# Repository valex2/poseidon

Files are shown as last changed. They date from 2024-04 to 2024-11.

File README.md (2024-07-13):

# poseidon
Stanford Robosub 🏄‍♂️🐳🌊 Electrical Subsystem Repository

[Website](https://www.stanfordrobosub.org/)

# Important notes
## Thrusters
DO NOT RUN THRUSTERS AT FULL POWER FOR THE TIME BEING - 20 to 30% max

DO NOT RUN FOR MORE THAN 10 SECONDS WHILE OUTSIDE OF WATER

## Comms
We are using a Teensy 4.0 that communicates with the Orin over a serial port.

Use serial library in Python, and write as follows:
> portName.write(b"thruster_number delay_value")

### Thruster PWM Assignment
- 1100 us is full reverse thrust
- 1500 us is off
- 1900 us is full forward thrust

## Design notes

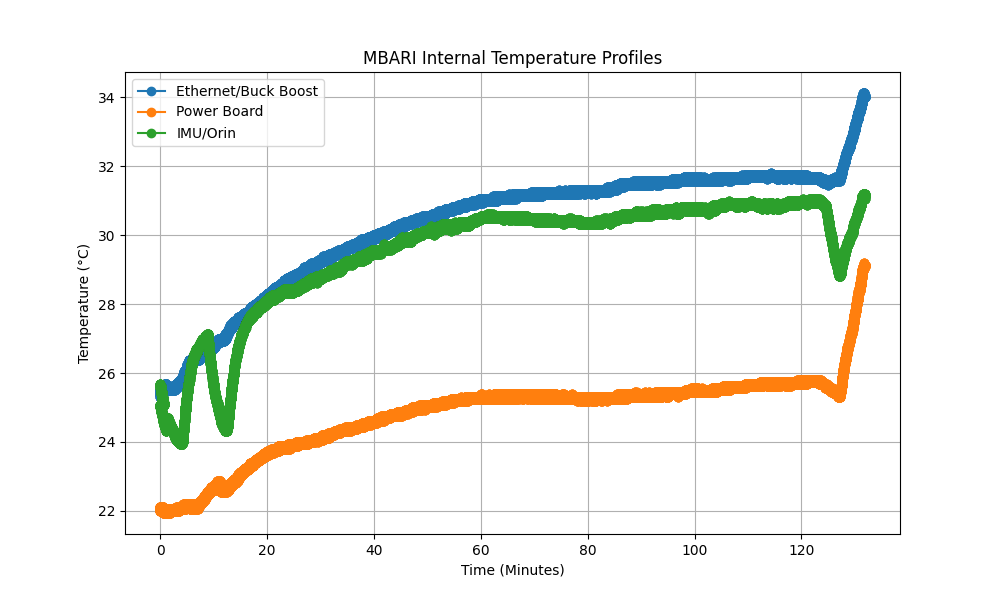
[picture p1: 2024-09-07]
CodeDev/MBARI_temperature_profiles.png

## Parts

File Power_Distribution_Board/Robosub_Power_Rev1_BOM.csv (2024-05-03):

# | Reference | Qty | Value | Footprint | DNP | Supplier 1 | Supplier 1 S/N | MFR | MFR S/N
1 | C1, C2 | 4 | 0.1u | Capacitor_SMD:C_0805_2012Metric_Pad1.18x1.45mm_HandSolder |  | https://www.digikey.com/en/products/detail/yageo/CC0805KRX7R9BB104/302874 | 311-1140-1-ND | YAGEO | CC0805KRX7R9BB104
2 | C3, C4 | 4 | 1uF | Capacitor_SMD:C_1812_4532Metric_Pad1.57x3.40mm_HandSolder |  | https://www.digikey.com/en/products/detail/knowles-syfer/1812Y2000105KSTWS2/18879756 | 1608-1812Y2000105KSTWS2CT-ND | Knowles Syfer | 1812Y2000105KSTWS2
3 | C5, C6 | 4 | 1u (electrolytic) | Robosub Lib:UCB1V0R1MCL1GS |  | https://www.digikey.com/en/products/detail/nichicon/UCB1V0R1MCL1GS/3974069 | 493-9956-1-ND | Nichicon | UCB1V0R1MCL1GS
4 | CR1 | 2 | SBRT15U50SP5-13 | SBRT15U50SP5_13:POWERDI5_DIO |  | https://www.digikey.com/en/products/detail/diodes-incorporated/SBRT15U50SP5-13/4567773 | SBRT15U50SP5-13DICT-ND | Diodes Incorporated | SBRT15U50SP5-13
5 | D1 | 2 | 1SMA5931BT3 | Diode_SMD:D_SMA |  | https://www.digikey.com/en/products/detail/onsemi/SZ1SMA5931BT3G/8538966 | SZ1SMA5931BT3GOSCT-ND | onsemi | SZ1SMA5931BT3G
6 | D2, D3 | 4 | IR26-21C_L110_TR8 | LED_SMD:LED_1206_3216Metric |  | https://www.digikey.com/en/products/detail/everlight-electronics-co-ltd/ir26-21c-l110-tr8/2675848 | 1080-1357-1-ND | Everlight Electronics Co Ltd | IR26-21C/L110/TR8
7 | H1, H2, H3, H4 | 8 | MountingHole | MountingHole:MountingHole_3.2mm_M3
8 | J1, J2, J3, J4, J5, J6, J7, J8, J9, J10 | 14 | 1135333 | 1135333_1:PHOENIX_1135333 |  | https://www.digikey.com/en/products/detail/phoenix-contact/1135333/17936877 | 277-1135333CT-ND | Pheonix Contact | SPT-THR 2,5/ 2-V-5,0 P20 R32
9 | J14 | 2 | Conn_01x04 | Connector_PinHeader_2.54mm:PinHeader_1x04_P2.54mm_Vertical
10 | JP4, JP5 | 4 | SolderJumper_2_Open | Jumper:SolderJumper-2_P1.3mm_Open_Pad1.0x1.5mm
11 | L1 | 2 | 74477420 | Robosub Lib:IND_5848-WE-PD2_WRE |  | https://www.digikey.com/en/products/detail/würth-elektronik/74477420/1638683 | 732-1278-1-ND | Würth Elektronik | 74477420
12 | R1, R3, R4 | 6 | 10k | Resistor_SMD:R_0805_2012Metric_Pad1.20x1.40mm_HandSolder |  | https://www.digikey.com/en/products/detail/yageo/RC0805FR-0710KL/727535 | 311-10.0KCRCT-ND | YAGEO | RC0805FR-0710KL
13 | R2 | 2 | 3k | Resistor_SMD:R_0805_2012Metric_Pad1.20x1.40mm_HandSolder |  | https://www.digikey.com/en/products/detail/te-connectivity-passive-product/CRG0805F3K0/2380900 | A126368CT-ND | TE Connectivity Passive Product | CRG0805F3K0
14 | R5 | 2 | 10 | Resistor_SMD:R_0805_2012Metric_Pad1.20x1.40mm_HandSolder |  | https://www.digikey.com/en/products/detail/yageo/RC0805FR-0710RL/727534 | 311-10.0CRCT-ND | YAGEO | RC0805FR-0710RL
15 | R6, R7, R8 | 6 | 100 | Resistor_SMD:R_0805_2012Metric_Pad1.20x1.40mm_HandSolder |  | https://www.digikey.com/en/products/detail/yageo/RC0805FR-07100RL/727543 | 311-100CRCT-ND | YAGEO | RC0805FR-07100RL
16 | R9 | 2 | 0 (100A) | Resistor_SMD:R_2512_6332Metric_Pad1.40x3.35mm_HandSolder |  | https://www.digikey.com/en/products/detail/bourns-inc./CSS2H-2512C-000E/16357993?gad_source=1 | 118-CSS2H-2512C-000ECT-ND | Bourns Inc. | CSS2H-2512C-000E
17 | U1 | 2 | INA300AIDSQT | Robosub Lib:SON40P200X200X80-11N |  | https://www.digikey.com/en/products/detail/texas-instruments/INA300AIDSQT/4759519 | 296-37474-1-ND | Texas Instruments | INA300AIDSQT
18 | U2 | 2 | SN74LVC1G97DBVR | Robosub Lib:SOT95P280X145-6N |  | https://www.digikey.com/en/products/detail/texas-instruments/SN74LVC1G97DBVR/571196 | 296-15581-1-ND | Texas Instruments | SN74LVC1G97DBVR
19 | U3 | 2 | AUIR3241STR | Robosub Lib:SOIC127P600X175-8N_AUIR3241STR |  | https://www.digikey.com/en/products/detail/infineon-technologies/auir3241str/7428056 | AUIR3241SCT-ND | Infineon Technologies | AUIR3241STR
20 | U4, U5, U6 | 6 | BSC0702LSATMA1 | Robosub Lib:BSC0702LSATMA1 |  | https://www.digikey.com/en/products/detail/infineon-technologies/BSC0702LSATMA1/7323968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 | 448-BSC0702LSATMA1CT-ND | Infineon Technologies | BSC0702LSATMA1
21 | U7, U8 | 3 | NVTR01P02LT1G | Robosub Lib:SOT-23-3_1P4X3P040_ONS |  | https://www.digikey.com/en/products/detail/onsemi/NVTR01P02LT1G/3062562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 | NVTR01P02LT1GOSCT-ND | onsemi | NVTR01P02LT1G
22 | WSLP59312L000FEA_1, WSLP59312L000FEA_2 | 4 | 2mOhm | WSLP59312L000FEA:RES_WSLP5931_.002OHM_VIS |  | https://www.digikey.com/en/products/detail/vishay-dale/WSLP59312L000FEA/5215934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 | 541-10013-1-ND | Vishay Dale | WSLP59312L000FEA
23 | Hall effect | 1 |  |  |  | https://www.digikey.com/en/products/detail/littelfuse-inc/55140-3H-02-A/565513 | 55140-3H-02-A-ND | Littelfuse Inc. | 55140-3H-02-A
24 | Magnet | 1 |  |  |  | https://www.digikey.com/en/products/detail/littelfuse-inc/H-58-MAGNET/10269030 | F12127-ND | Littelfuse Inc. | H-58-MAGNET

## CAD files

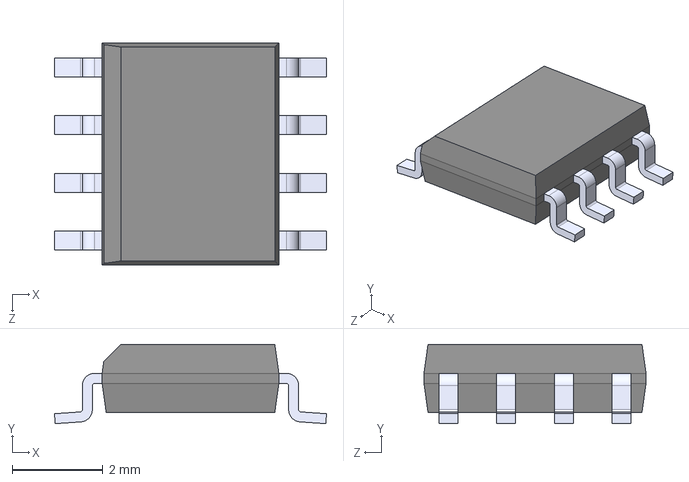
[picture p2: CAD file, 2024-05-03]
Power_Distribution_Board/EDA/AUIR3241STR/AUIR3241STR.step
6.00 x 1.75 x 4.90 mm

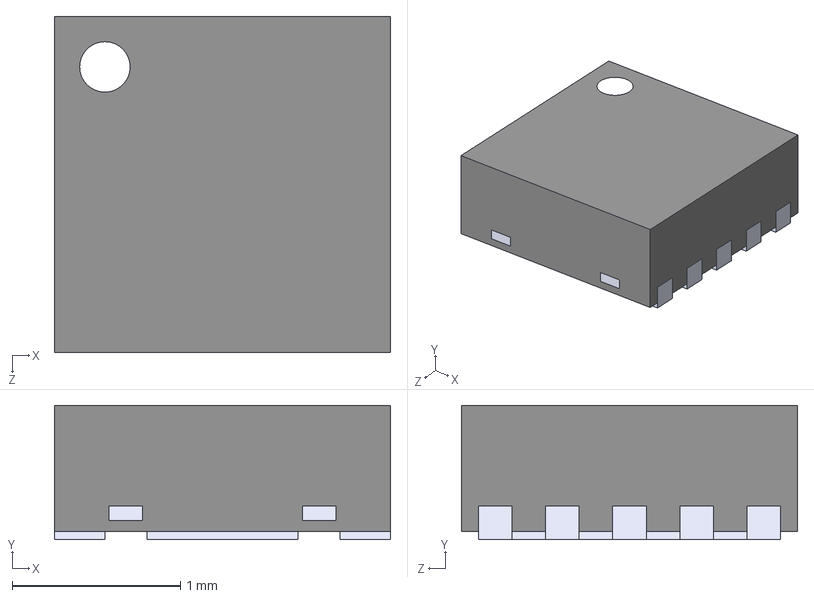
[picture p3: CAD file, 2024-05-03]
Power_Distribution_Board/EDA/INA300AIDSQT/INA300AIDSQT.step
2.00 x 0.8 x 2.00 mm

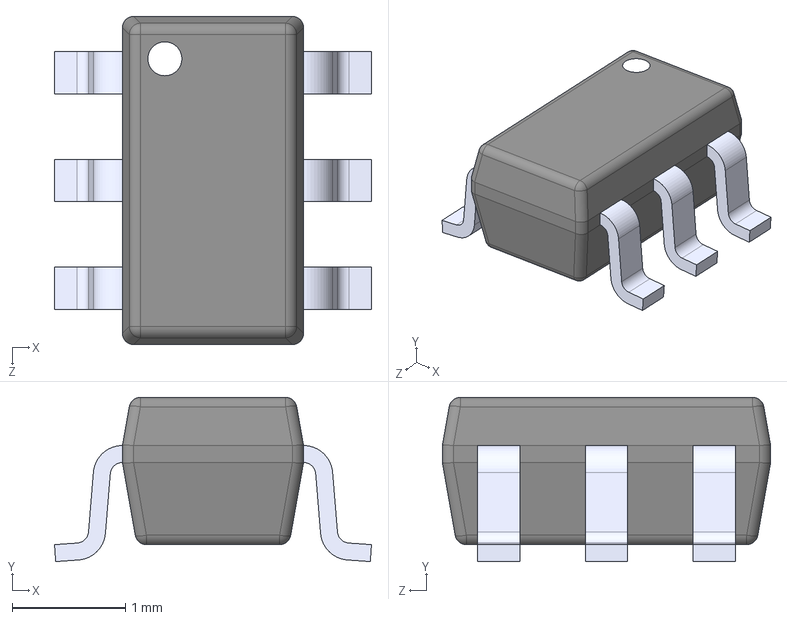
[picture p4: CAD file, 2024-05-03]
Power_Distribution_Board/EDA/SN74LVC1G97DBVR/SN74LVC1G97DBVR.step
2.80 x 1.45 x 2.90 mm

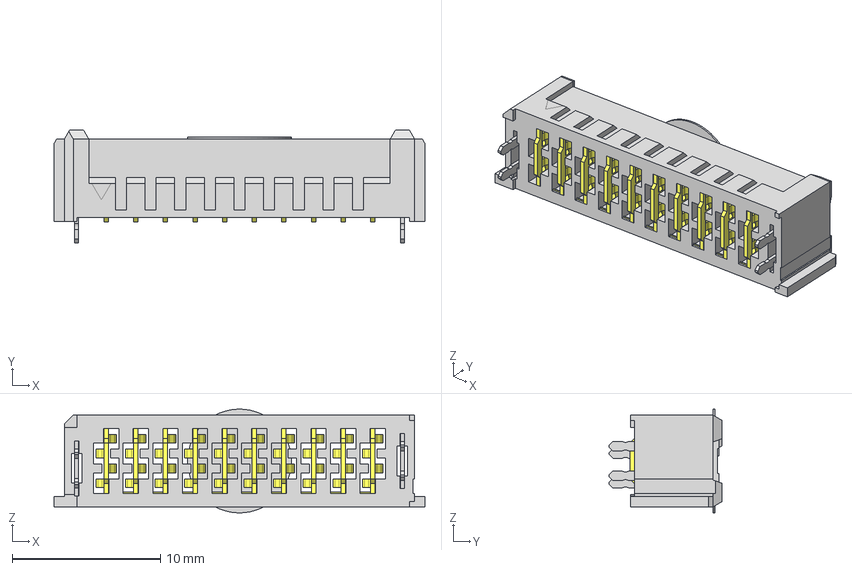
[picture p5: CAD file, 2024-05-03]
Power_Distribution_Board/EDA/UMPS_10_05_5_L_V_S_W_TR/UMPS-10-05.5-L-V-S-W-TR.step
25.1 x 7.60 x 7.01 mm
10-05.5--W_BODY
UMPS-10-05.5-S_PINS
10-05.5-S_PINS2
K-DOT-0.276-.005_KAPTON

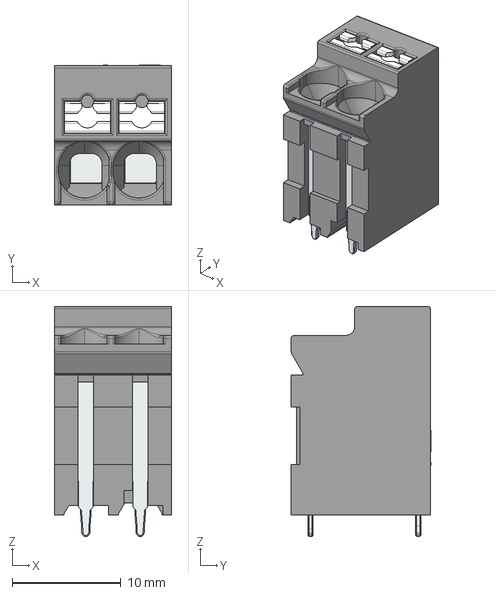
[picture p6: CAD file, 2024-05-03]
Power_Distribution_Board/EDA/1135333/1135333.step
10.8 x 12.8 x 21.2 mm

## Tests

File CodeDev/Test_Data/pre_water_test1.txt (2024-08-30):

1472,22.75,21.94,21.94
1541,22.75,21.94,21.94
1592,22.75,21.94,21.94
1642,22.75,21.94,21.94
1693,22.75,21.94,21.94
1743,22.75,21.94,21.94
1794,22.75,21.94,21.94
1844,22.75,21.94,21.94
1895,22.75,21.94,21.94
1945,22.75,21.94,21.94
1996,22.75,21.94,21.94
2046,22.75,21.94,21.94
2097,22.75,21.94,21.94
2147,22.75,21.94,21.94
2198,22.75,22.00,21.94
2248,22.75,22.00,21.94
2299,22.75,22.00,21.94
2349,22.75,22.00,21.94
2400,22.75,22.00,21.94
2450,22.81,21.94,21.94
2500,22.81,21.94,21.94
2551,22.81,21.94,21.94
2601,22.81,21.94,21.94
2652,22.81,21.94,21.94
2701,22.75,22.00,21.94
2752,22.75,22.00,21.94
2807,22.75,22.00,21.94
2858,22.75,22.00,21.94
2908,22.75,22.00,21.94
2958,22.75,21.94,21.94
3008,22.75,21.94,21.94
3058,22.75,21.94,21.94
3108,22.75,21.94,21.94
3159,22.75,21.94,21.94
3209,22.75,21.94,21.94
3259,22.75,21.94,21.94
3309,22.75,21.94,21.94
3359,22.75,21.94,21.94
3410,22.81,21.94,21.94
3460,22.81,22.00,21.94
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

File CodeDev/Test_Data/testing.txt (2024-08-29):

2515,25.31,24.94,25.12
2584,25.31,24.94,25.12
2634,25.31,24.94,25.12
2687,25.31,24.94,25.12
2737,25.31,24.94,25.12
2788,25.31,24.94,25.12
2838,25.31,24.94,25.12
2890,25.31,24.94,25.12
2941,25.31,24.94,25.12
2991,25.31,24.94,25.12
3042,25.31,24.88,25.12
3093,25.31,24.88,25.12
3143,25.31,24.88,25.12
3194,25.31,24.88,25.12
3245,25.31,24.88,25.12
3295,25.25,24.88,25.12
3346,25.25,24.88,25.12
3396,25.25,24.88,25.12
3447,25.25,24.88,25.12
3498,25.25,24.88,25.12
3548,25.31,24.94,25.12
3599,25.31,24.94,25.12
3649,25.31,24.94,25.19
3700,25.31,24.94,25.19
3750,25.31,24.94,25.19
3800,25.31,24.94,25.19
3851,25.31,24.94,25.19
3906,25.31,24.94,25.12
3957,25.31,24.94,25.12
4008,25.25,24.94,25.12
4058,25.25,24.88,25.12
4108,25.25,24.88,25.12
4159,25.25,24.88,25.12
4209,25.25,24.88,25.12
4260,25.25,24.88,25.12
4310,25.25,24.88,25.12
4360,25.25,24.88,25.12
4410,25.25,24.88,25.12
4461,25.25,24.88,25.12
4511,25.31,24.88,25.12
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

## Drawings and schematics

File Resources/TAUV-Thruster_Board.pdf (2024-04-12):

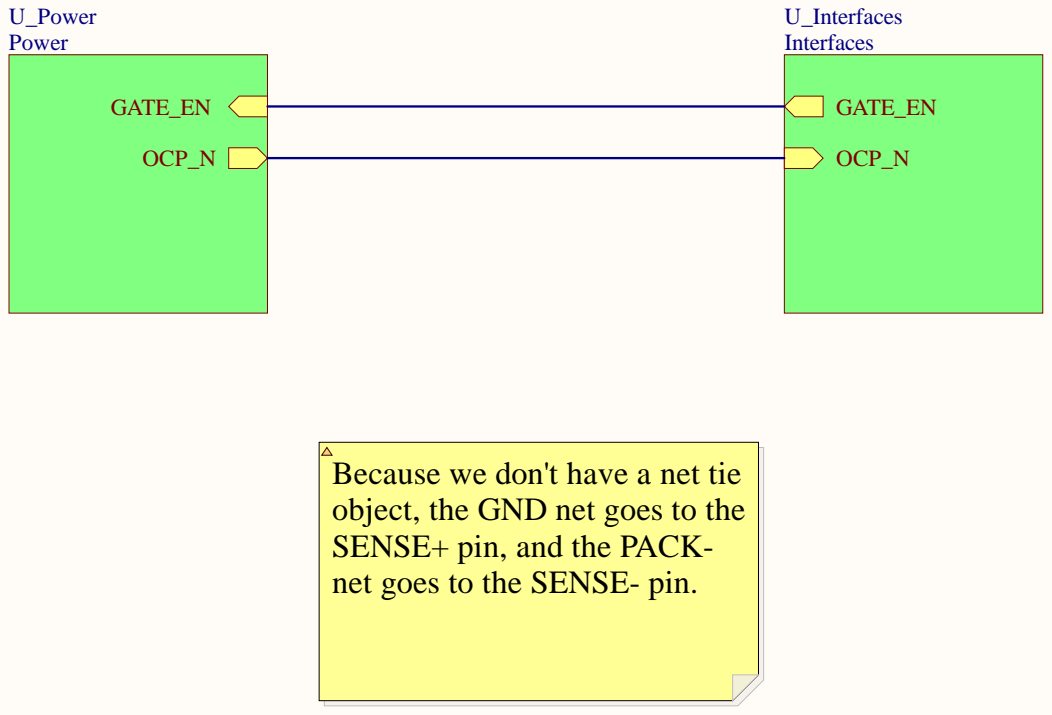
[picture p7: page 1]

Because we don't have a net tie
object, the GND net goes to the
SENSE+ pin, and the PACK-
net goes to the SENSE- pin.

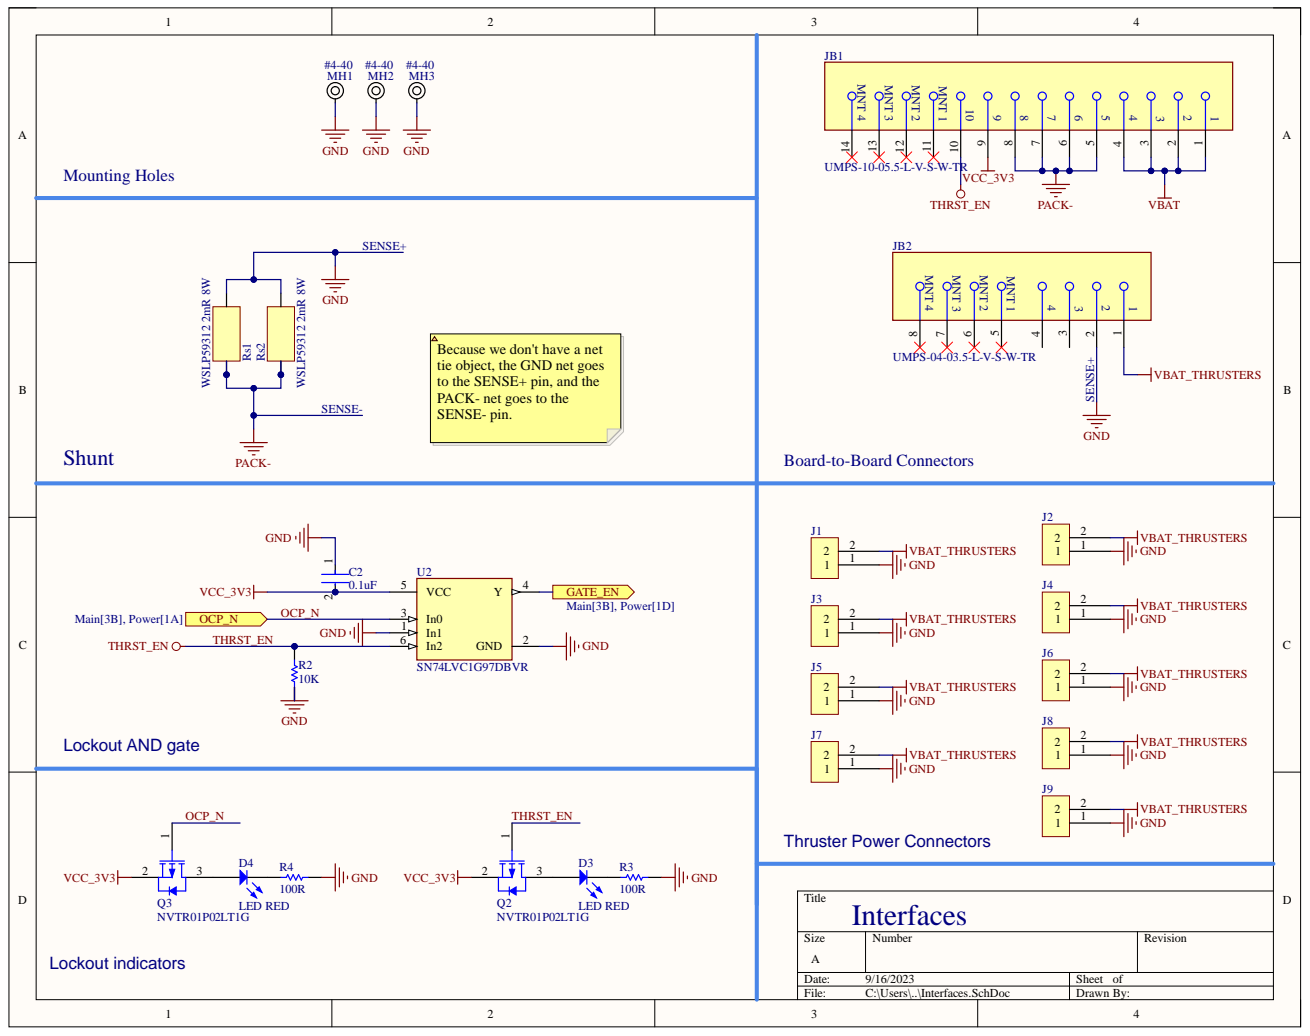
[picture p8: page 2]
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

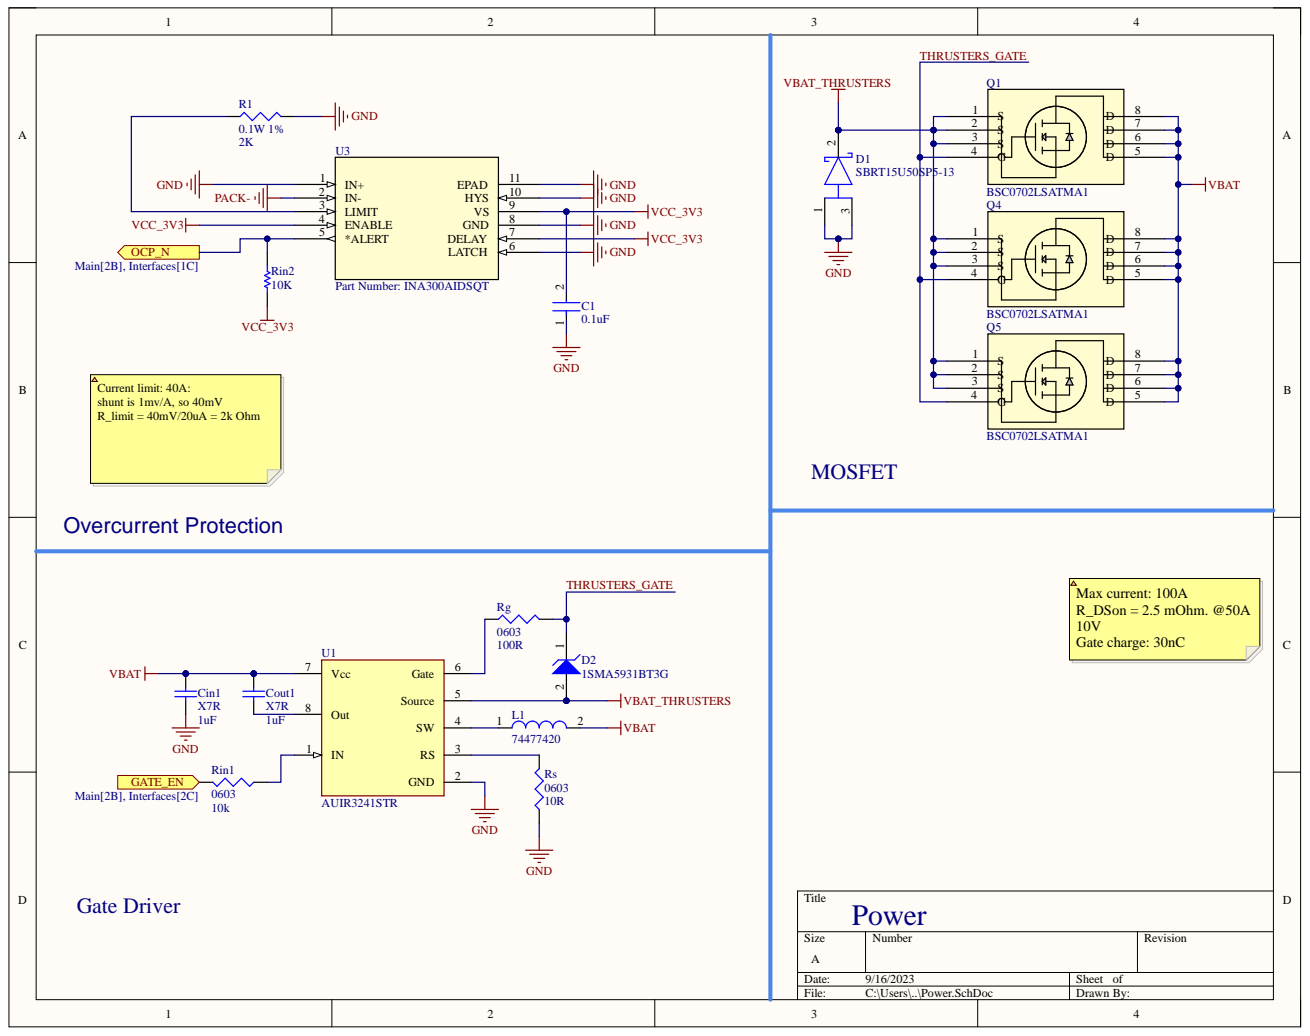
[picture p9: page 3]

LIMIT 3

*ALERT 5

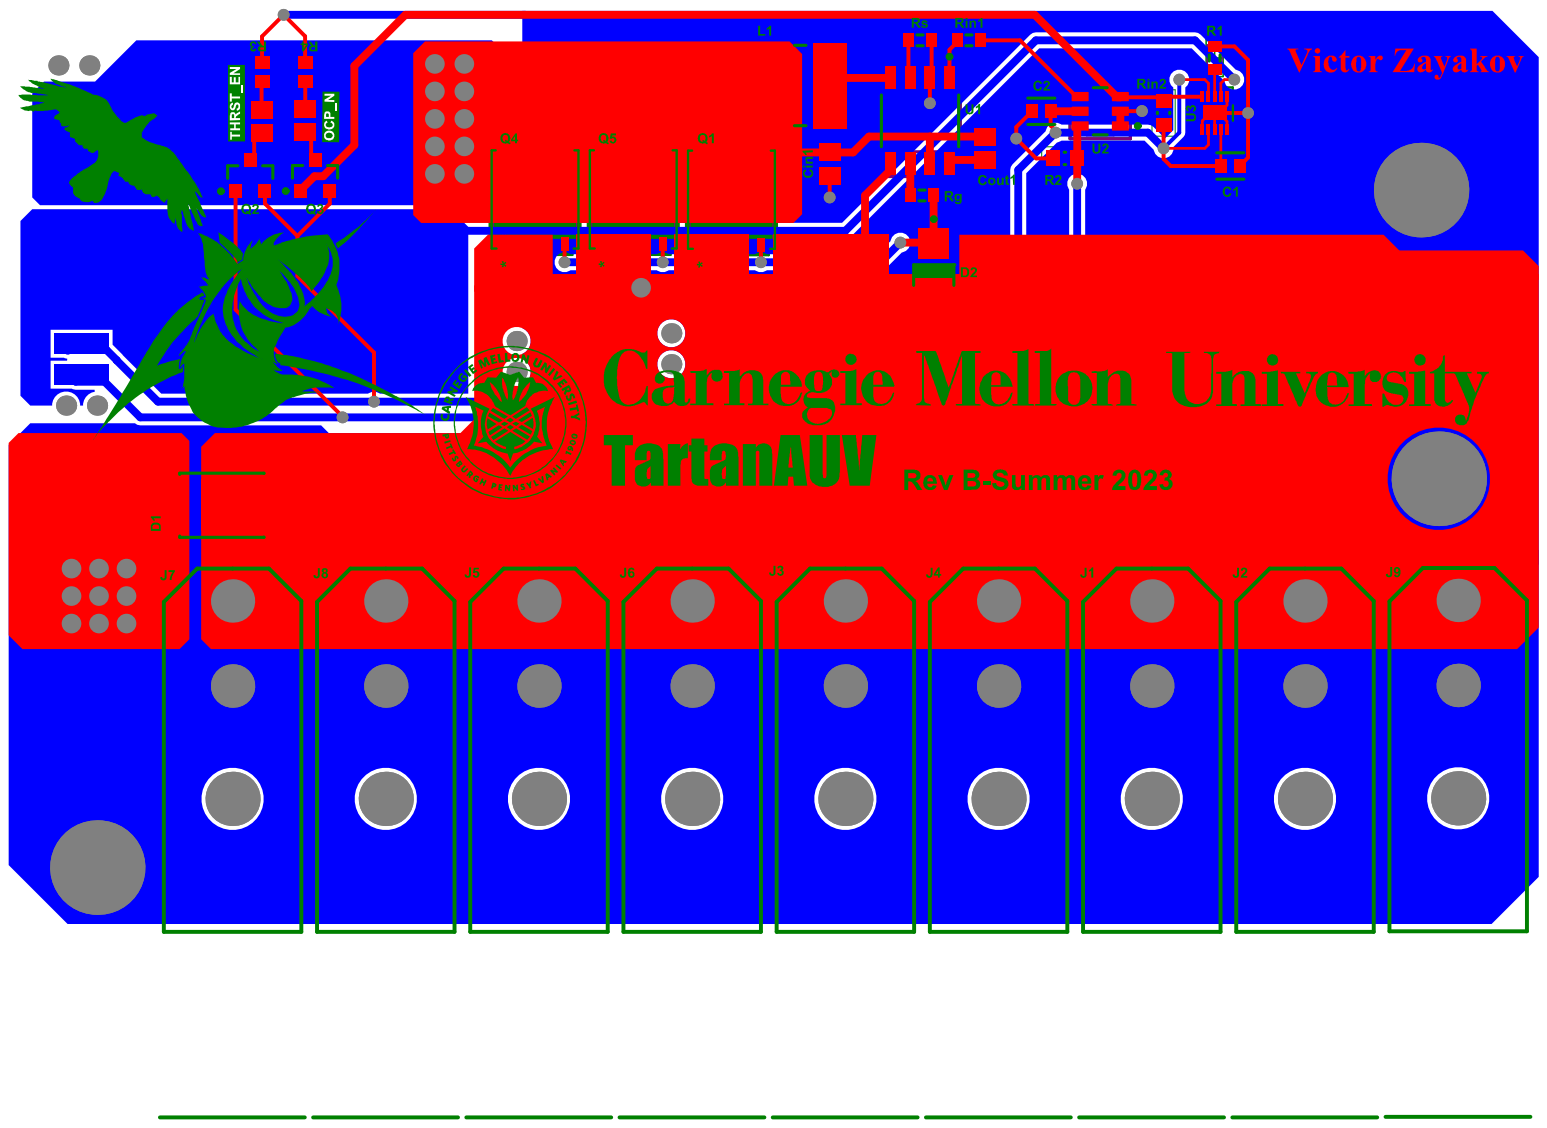
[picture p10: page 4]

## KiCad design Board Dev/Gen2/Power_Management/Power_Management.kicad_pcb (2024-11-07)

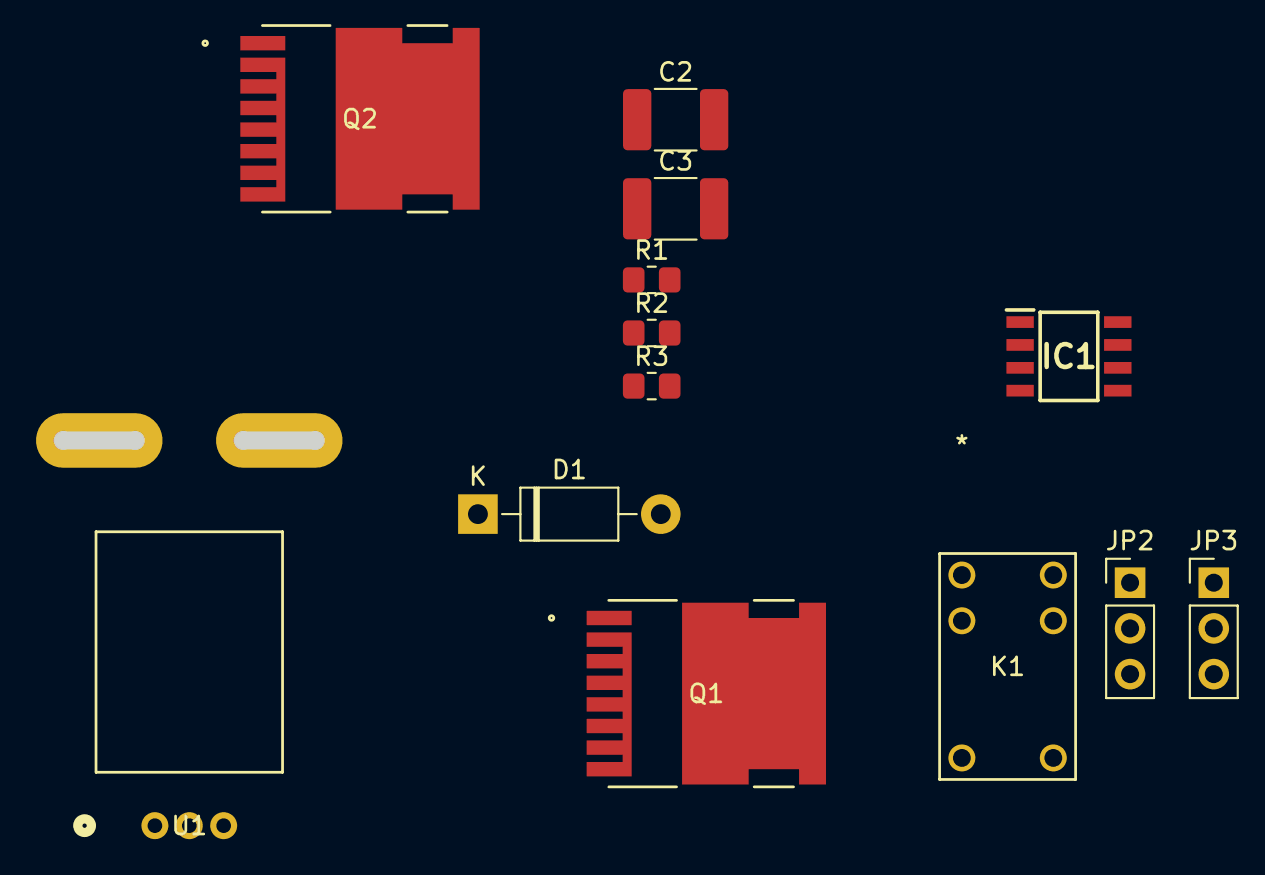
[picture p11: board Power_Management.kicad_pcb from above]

Board: 2 copper layers, 13 parts (0 on the bottom side), 9 nets, no tracks yet.

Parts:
C2, C3: 1uF; C_1812_4532Metric_Pad1.57x3.40mm_HandSolder
D1: 1N5819; D_DO-41_SOD81_P10.16mm_Horizontal
IC1: MC33063AQDRQ1; SOIC127P600X175-8N
JP2, JP3: Jumper_3_Bridged12; PinHeader_1x03_P2.54mm_Vertical
K1: G5V-1 DC3; RELAY_G5V-1_OMR
Q1, Q2: MCTL160N15Y-TP; TOLL-8L_MCC
R1: 10k; R_0805_2012Metric_Pad1.20x1.40mm_HandSolder
R2: 10; R_0805_2012Metric_Pad1.20x1.40mm_HandSolder
R3: 100; R_0805_2012Metric_Pad1.20x1.40mm_HandSolder
U1: ACS758ECB-200U-PFF-T; PFF_ACS758ECB-200U-PFF-T_ALM

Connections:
+25V: D1.1 (K), JP2.1 (A), JP3.3 (B)
+BATT: IC1.6 (VCC), Q1.9 (D), Q2.9 (D), U1.5 (IP-)
-BATT: IC1.2 (SWITCH_EMITTER), IC1.4 (GND), JP2.3 (B), JP3.1 (A), Q1.2 (S), Q1.3 (S), Q1.4 (S), Q1.5 (S), Q1.6 (S), Q1.7 (S), Q1.8 (S), Q2.2 (S), Q2.3 (S), Q2.4 (S), Q2.5 (S), Q2.6 (S), Q2.7 (S), Q2.8 (S)
GATE_DRIVE: K1.5, K1.6, Q1.1 (G), Q2.1 (G)
GND: C3.2, K1.9, R2.2, U1.2 (GND)
unnamed: D1.2 (A), IC1.1 (SWITCH_COLLECTOR)
unnamed: JP2.2 (C), K1.10
unnamed: JP3.2 (C), K1.1
Sense(+): C2.1, C3.1

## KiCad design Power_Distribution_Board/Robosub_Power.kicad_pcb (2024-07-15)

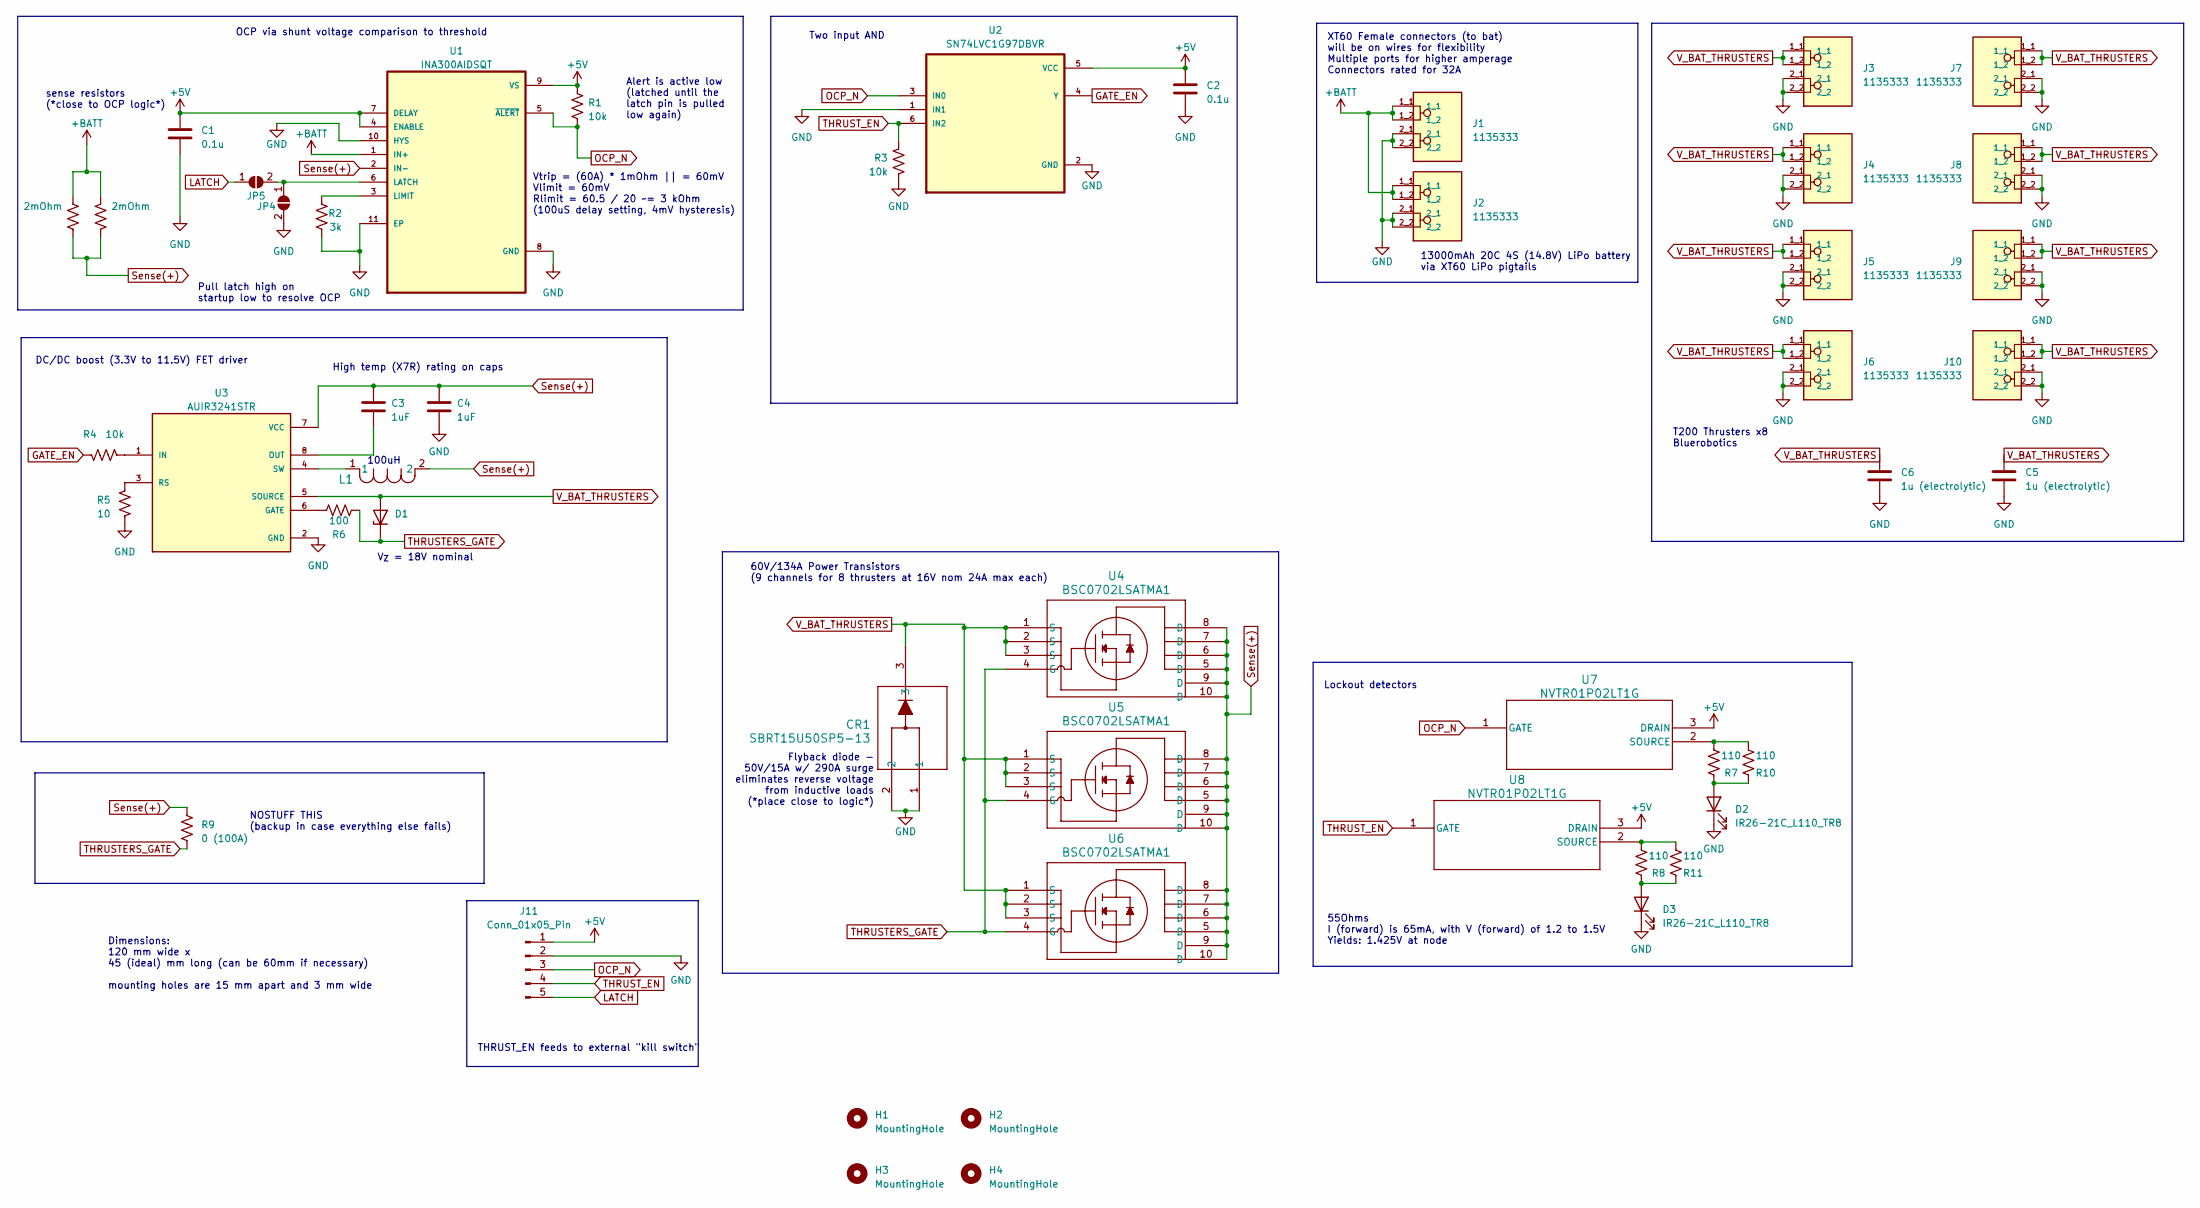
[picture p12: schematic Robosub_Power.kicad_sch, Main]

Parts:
C1, C2: 0.1u; C_0805_2012Metric_Pad1.18x1.45mm_HandSolder
C3, C4: 1uF; C_1812_4532Metric_Pad1.57x3.40mm_HandSolder
C5, C6: 1u (electrolytic); UCB1V0R1MCL1GS
CR1: SBRT15U50SP5-13; POWERDI5_DIO
D1: 1SMA5931BT3; D_SMA
D2, D3: IR26-21C_L110_TR8; LED_1206_3216Metric
H1, H2, H3, H4: MountingHole; MountingHole_3.2mm_M3
J1, J2, J3, J4, J5, J6, J7, J8, J9, J10: 1135333; PHOENIX_1135333
J11: Conn_01x05_Pin; PinHeader_1x05_P2.54mm_Vertical
JP4, JP5: SolderJumper_2_Open; SolderJumper-2_P1.3mm_Open_Pad1.0x1.5mm
L1: 74477420; IND_5848-WE-PD2_WRE
R1, R3, R4: 10k; R_0805_2012Metric_Pad1.20x1.40mm_HandSolder
R2: 3k; R_0805_2012Metric_Pad1.20x1.40mm_HandSolder
R5: 10; R_0805_2012Metric_Pad1.20x1.40mm_HandSolder
R6: 100; R_0805_2012Metric_Pad1.20x1.40mm_HandSolder
R7, R8, R10, R11: 110; R_0805_2012Metric_Pad1.20x1.40mm_HandSolder
R9: 0 (100A); R_2512_6332Metric_Pad1.40x3.35mm_HandSolder
U1: INA300AIDSQT; SON40P200X200X80-11N
U2: SN74LVC1G97DBVR; SOT95P280X145-6N
U3: AUIR3241STR; SOIC127P600X175-8N_AUIR3241STR
U4, U5, U6: BSC0702LSATMA1
U7, U8: NVTR01P02LT1G; SOT-23-3_1P4X3P040_ONS
WSLP59312L000FEA_1, WSLP59312L000FEA_2: 2mOhm; RES_WSLP5931_.002OHM_VIS

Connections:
+5V: C1.1, C2.1, J11.1, R1.1, U1.4 (ENABLE), U1.7 (DELAY), U1.9 (VS), U2.5 (VCC), U7.3 (DRAIN), U8.3 (DRAIN)
+BATT: J1.1_1, J1.1_2, J2.1_1, J2.1_2, U1.1 (IN+), WSLP59312L000FEA_1.2, WSLP59312L000FEA_2.2
GATE_EN: R4.1, U2.4 (Y)
GND: C1.2, C2.2, C4.2, C5.2, C6.2, CR1.1, CR1.2, D2.1 (K), D3.1 (K), J1.2_1, J1.2_2, J2.2_1, J2.2_2, J3.2_1, J3.2_2, J4.2_1, J4.2_2, J5.2_1, J5.2_2, J6.2_1, J6.2_2, J7.2_1, J7.2_2, J8.2_1, J8.2_2, J9.2_1, J9.2_2, J10.2_1, J10.2_2, J11.2, JP4.2 (B), R2.2, R3.2, R5.2, U1.8 (GND), U1.10 (HYS), U1.11 (EP), U2.1 (IN1), U2.2 (GND), U3.2 (GND)
LATCH: J11.5, JP5.1 (A)
unnamed: D2.2 (A), R7.1, R10.1
unnamed: D3.2 (A), R8.1, R11.1
unnamed: JP4.1 (A), JP5.2 (B), U1.6 (LATCH)
unnamed: R2.1, U1.3 (LIMIT)
unnamed: R6.1, U3.6 (GATE)
unnamed: R4.2, U3.1 (IN)
unnamed: C3.2, U3.8 (OUT)
unnamed: R5.1, U3.3 (RS)
unnamed: L1.1, U3.4 (SW)
unnamed: R7.2, R10.2, U7.2 (SOURCE)
unnamed: R8.2, R11.2, U8.2 (SOURCE)
OCP_N: J11.3, R1.2, U1.5 (~ALERT), U2.3 (IN0), U7.1 (GATE)
Sense(+): C3.1, C4.1, L1.2, R9.1, U1.2 (IN-), U3.7 (VCC), U4.5 (D), U4.6 (D), U4.7 (D), U4.8 (D), U4.9 (D), U4.10 (D), U5.5 (D), U5.6 (D), U5.7 (D), U5.8 (D), U5.9 (D), U5.10 (D), U6.5 (D), U6.6 (D), U6.7 (D), U6.8 (D), U6.9 (D), U6.10 (D), WSLP59312L000FEA_1.1, WSLP59312L000FEA_2.1
THRUSTERS_GATE: D1.1 (K), R6.2, R9.2, U4.4 (G), U5.4 (G), U6.4 (G)
THRUST_EN: J11.4, R3.1, U2.6 (IN2), U8.1 (GATE)
V_BAT_THRUSTERS: C5.1, C6.1, CR1.3, D1.2 (A), J3.1_1, J3.1_2, J4.1_1, J4.1_2, J5.1_1, J5.1_2, J6.1_1, J6.1_2, J7.1_1, J7.1_2, J8.1_1, J8.1_2, J9.1_1, J9.1_2, J10.1_1, J10.1_2, U3.5 (SOURCE), U4.1 (S), U4.2 (S), U4.3 (S), U5.1 (S), U5.2 (S), U5.3 (S), U6.1 (S), U6.2 (S), U6.3 (S)

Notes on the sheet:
THRUST_EN feeds to external "kill switch"
Two input AND
Lockout detectors
Dimensions: 120 mm wide x 45 (ideal) mm long (can be 60mm if necessary) mounting holes are 15 mm apart and 3 mm wide
High temp (X7R) rating on caps
13000mAh 20C 4S (14.8V) LiPo battery via XT60 LiPo pigtails
Vtrip = (60A) * 1mOhm || = 60mV Vlimit = 60mV Rlimit = 60.5 / 20 ~= 3 kOhm (100uS delay setting, 4mV hysteresis)
Alert is active low (latched until the latch pin is pulled low again)
DC/DC boost (3.3V to 11.5V) FET driver
55Ohms I (forward) is 65mA, with V (forward) of 1.2 to 1.5V Yields: 1.425V at node
XT60 Female connectors (to bat) will be on wires for flexibility Multiple ports for higher amperage Connectors rated for 32A
Flyback diode - 50V/15A w/ 290A surge eliminates reverse voltage from inductive loads (*place close to logic*)
60V/134A Power Transistors (9 channels for 8 thrusters at 16V nom 24A max each)
V_{Z} = 18V nominal
100uH
NOSTUFF THIS (backup in case everything else fails)
T200 Thrusters x8 Bluerobotics
OCP via shunt voltage comparison to threshold
Pull latch high on startup low to resolve OCP
sense resistors (*close to OCP logic*)

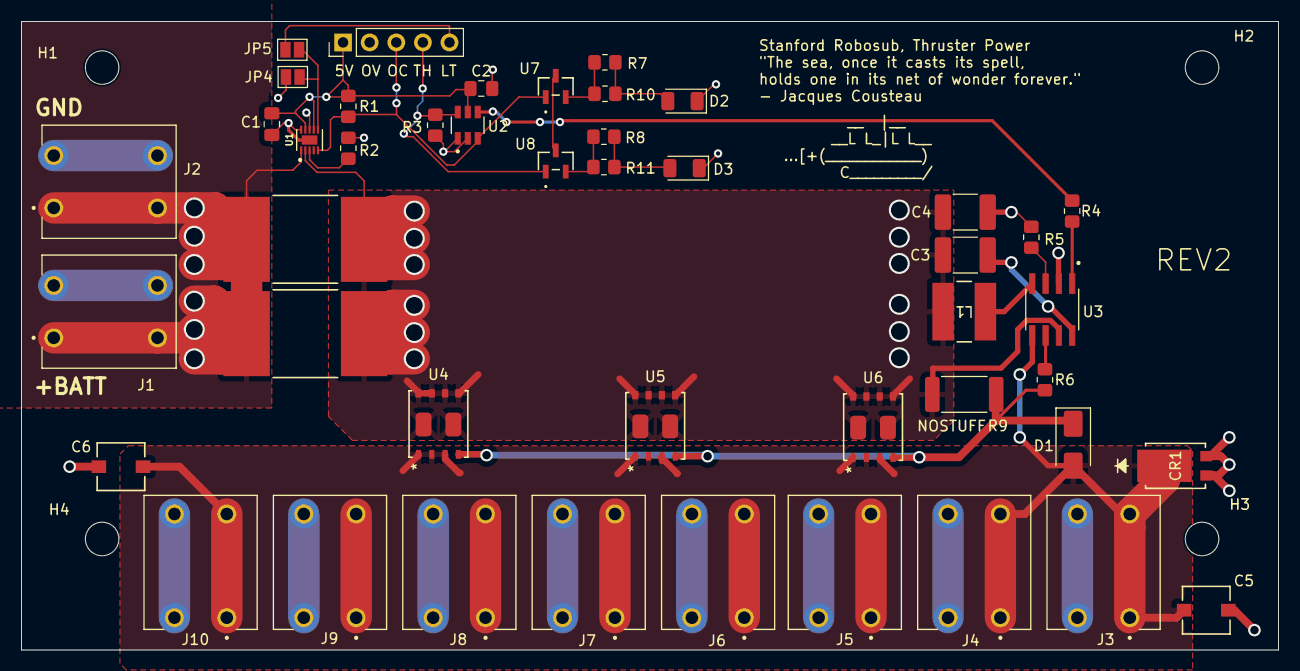
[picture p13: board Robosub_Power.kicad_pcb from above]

Board: 2 copper layers, 120.0 x 60.0 mm, 49 parts (0 on the bottom side), 21 nets.

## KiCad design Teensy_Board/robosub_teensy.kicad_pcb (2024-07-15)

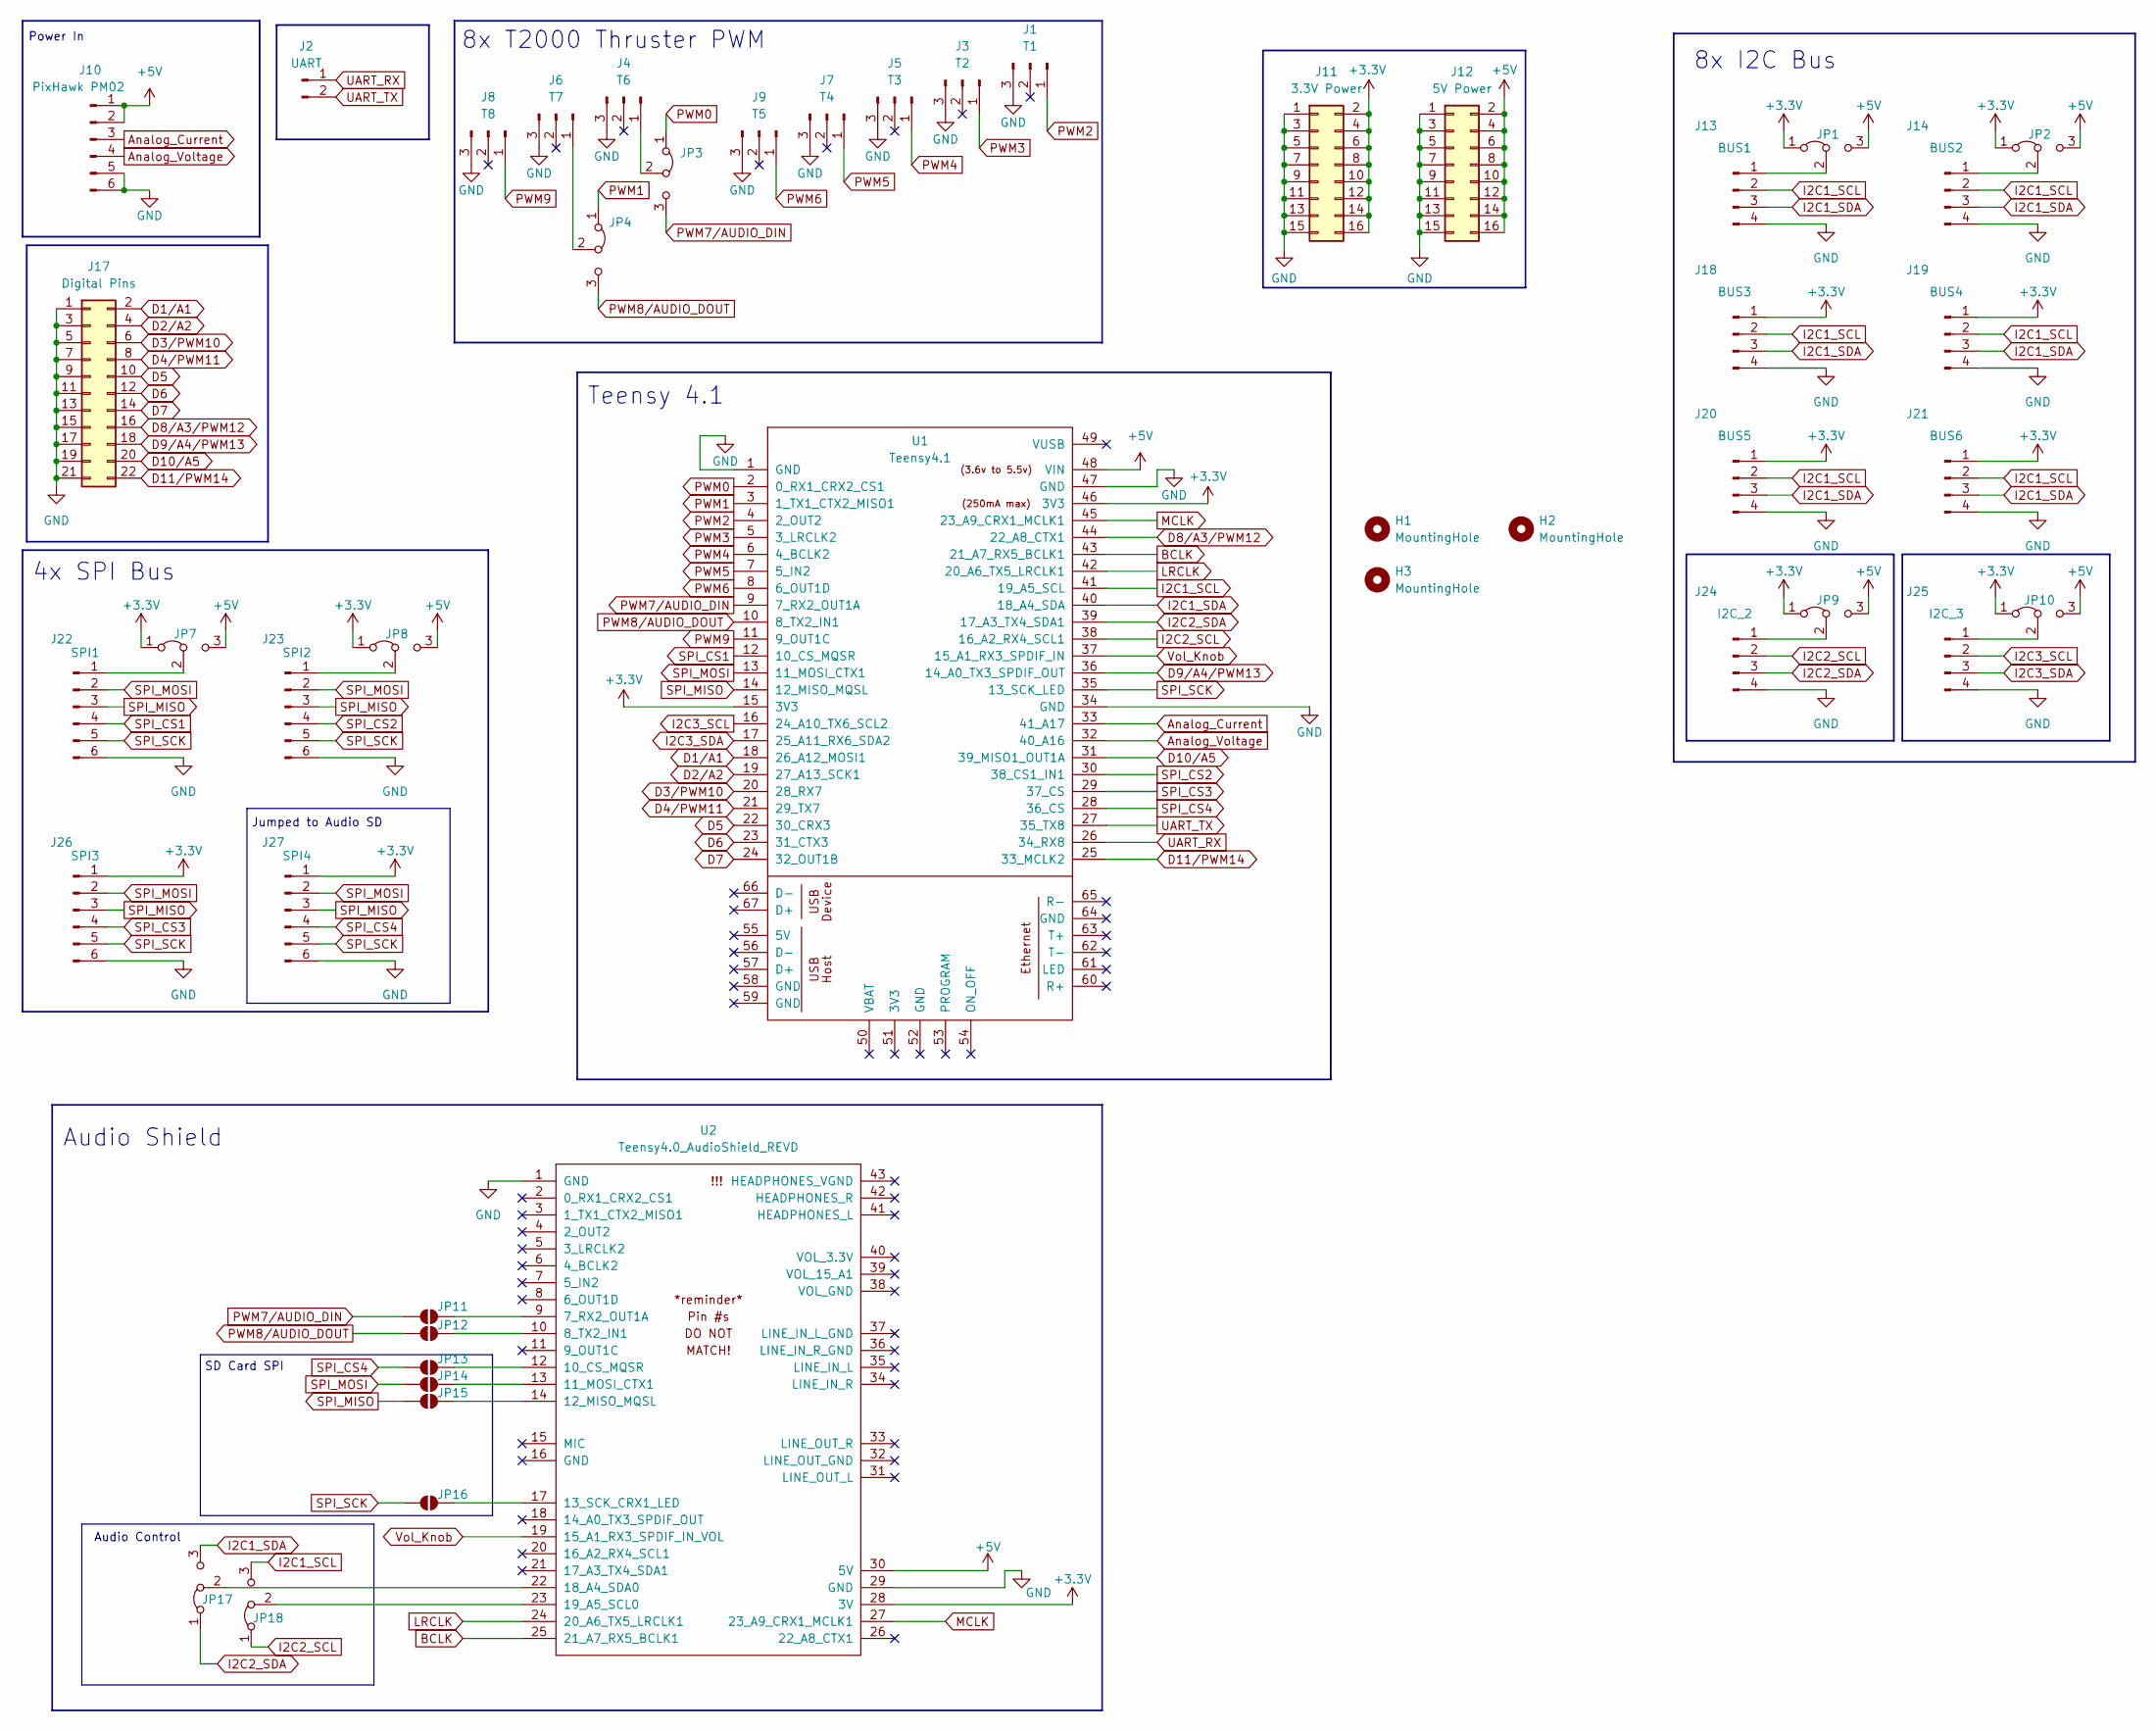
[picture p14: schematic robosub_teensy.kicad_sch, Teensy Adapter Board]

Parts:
H1, H2, H3: MountingHole; MountingHole_3.2mm_M3
J1: T1; PinSocket_1x03_P2.54mm_Vertical
J2: UART; PinSocket_1x02_P2.54mm_Vertical
J3: T2; PinSocket_1x03_P2.54mm_Vertical
J4: T6; PinSocket_1x03_P2.54mm_Vertical
J5: T3; PinSocket_1x03_P2.54mm_Vertical
J6: T7; PinSocket_1x03_P2.54mm_Vertical
J7: T4; PinSocket_1x03_P2.54mm_Vertical
J8: T8; PinSocket_1x03_P2.54mm_Vertical
J9: T5; PinSocket_1x03_P2.54mm_Vertical
J10: PixHawk PM02; PinSocket_1x06_P2.54mm_Vertical
J11: 3.3V Power; PinSocket_2x08_P2.54mm_Vertical
J12: 5V Power; PinSocket_2x08_P2.54mm_Vertical
J13: BUS1; PinSocket_1x04_P2.54mm_Vertical
J14: BUS2; PinSocket_1x04_P2.54mm_Vertical
J17: Digital Pins; PinSocket_2x11_P2.54mm_Vertical
J18: BUS3; PinSocket_1x04_P2.54mm_Vertical
J19: BUS4; PinSocket_1x04_P2.54mm_Vertical
J20: BUS5; PinSocket_1x04_P2.54mm_Vertical
J21: BUS6; PinSocket_1x04_P2.54mm_Vertical
J22: SPI1; PinSocket_1x06_P2.54mm_Vertical
J23: SPI2; PinSocket_1x06_P2.54mm_Vertical
J24: I2C_2; PinSocket_1x04_P2.54mm_Vertical
J25: I2C_3; PinSocket_1x04_P2.54mm_Vertical
J26: SPI3; PinSocket_1x06_P2.54mm_Vertical
J27: SPI4; PinSocket_1x06_P2.54mm_Vertical
JP1: BUS1_PWR; PinSocket_1x03_P2.54mm_Vertical
JP2: BUS2_PWR; PinSocket_1x03_P2.54mm_Vertical
JP3: T6_Sel; PinSocket_1x03_P2.54mm_Vertical
JP4: T7_Sel; PinSocket_1x03_P2.54mm_Vertical
JP7: SPI1_PWR; PinSocket_1x03_P2.54mm_Vertical
JP8: SPI2_PWR; PinSocket_1x03_P2.54mm_Vertical
JP9: I2C2_PWR; PinSocket_1x03_P2.54mm_Vertical
JP10: I2C3_PWR; PinSocket_1x03_P2.54mm_Vertical
JP11: AUDIO_DIN; SolderJumper-2_P1.3mm_Open_Pad1.0x1.5mm
JP12: AUDIO_DOUT; SolderJumper-2_P1.3mm_Open_Pad1.0x1.5mm
JP13: AUDIO_CS; SolderJumper-2_P1.3mm_Open_Pad1.0x1.5mm
JP14: AUDIO_MOSI; SolderJumper-2_P1.3mm_Open_Pad1.0x1.5mm
JP15: AUDIO_MISO; SolderJumper-2_P1.3mm_Open_Pad1.0x1.5mm
JP16: AUDIO_SCK; SolderJumper-2_P1.3mm_Open_Pad1.0x1.5mm
JP17: SDA_Sel; PinSocket_1x03_P2.54mm_Vertical
JP18: SCL_Sel; PinSocket_1x03_P2.54mm_Vertical
U1: Teensy4.1; Teensy41
U2: Teensy4.0_AudioShield_REVD; 4.0audioshield

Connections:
+3.3V: J11.2, J11.4, J11.6, J11.8, J11.10, J11.12, J11.14, J11.16, J18.1, J19.1, J20.1, J21.1, J26.1, J27.1, JP1.1 (A), JP2.1 (A), JP7.1 (A), JP8.1 (A), JP9.1 (A), JP10.1 (A), U1.15 (3V3), U1.46 (3V3), U2.28 (3V)
+5V: J10.1, J10.2, J12.2, J12.4, J12.6, J12.8, J12.10, J12.12, J12.14, J12.16, JP1.3 (B), JP2.3 (B), JP7.3 (B), JP8.3 (B), JP9.3 (B), JP10.3 (B), U1.48 (VIN), U2.30 (5V)
Analog_Current: J10.3, U1.33 (41_A17)
Analog_Voltage: J10.4, U1.32 (40_A16)
BCLK: U1.43 (21_A7_RX5_BCLK1), U2.25 (21_A7_RX5_BCLK1)
D1/A1: J17.2, U1.18 (26_A12_MOSI1)
D2/A2: J17.4, U1.19 (27_A13_SCK1)
D3/PWM10: J17.6, U1.20 (28_RX7)
D4/PWM11: J17.8, U1.21 (29_TX7)
D5: J17.10, U1.22 (30_CRX3)
D6: J17.12, U1.23 (31_CTX3)
D7: J17.14, U1.24 (32_OUT1B)
D8/A3/PWM12: J17.16, U1.44 (22_A8_CTX1)
D9/A4/PWM13: J17.18, U1.36 (14_A0_TX3_SPDIF_OUT)
D10/A5: J17.20, U1.31 (39_MISO1_OUT1A)
D11/PWM14: J17.22, U1.25 (33_MCLK2)
GND: J1.3, J3.3, J4.3, J5.3, J6.3, J7.3, J8.3, J9.3, J10.5, J10.6, J11.1, J11.3, J11.5, J11.7, J11.9, J11.11, J11.13, J11.15, J12.1, J12.3, J12.5, J12.7, J12.9, J12.11, J12.13, J12.15, J13.4, J14.4, J17.1, J17.3, J17.5, J17.7, J17.9, J17.11, J17.13, J17.15, J17.17, J17.19, J17.21, J18.4, J19.4, J20.4, J21.4, J22.6, J23.6, J24.4, J25.4, J26.6, J27.6, U1.1 (GND), U1.34 (GND), U1.47 (GND), U2.1 (GND), U2.29 (GND)
I2C1_SCL: J13.2, J14.2, J18.2, J19.2, J20.2, J21.2, JP18.3 (B), U1.41 (19_A5_SCL)
I2C1_SDA: J13.3, J14.3, J18.3, J19.3, J20.3, J21.3, JP17.3 (B), U1.40 (18_A4_SDA)
I2C2_SCL: J24.2, JP18.1 (A), U1.38 (16_A2_RX4_SCL1)
I2C2_SDA: J24.3, JP17.1 (A), U1.39 (17_A3_TX4_SDA1)
I2C3_SCL: J25.2, U1.16 (24_A10_TX6_SCL2)
I2C3_SDA: J25.3, U1.17 (25_A11_RX6_SDA2)
LRCLK: U1.42 (20_A6_TX5_LRCLK1), U2.24 (20_A6_TX5_LRCLK1)
MCLK: U1.45 (23_A9_CRX1_MCLK1), U2.27 (23_A9_CRX1_MCLK1)
unnamed: J4.1, JP3.2 (C)
unnamed: J6.1, JP4.2 (C)
unnamed: J13.1, JP1.2 (C)
unnamed: J14.1, JP2.2 (C)
unnamed: J22.1, JP7.2 (C)
unnamed: J23.1, JP8.2 (C)
unnamed: J24.1, JP9.2 (C)
unnamed: J25.1, JP10.2 (C)
unnamed: JP11.2 (B), U2.9 (7_RX2_OUT1A)
unnamed: JP12.2 (B), U2.10 (8_TX2_IN1)
unnamed: JP13.2 (B), U2.12 (10_CS_MQSR)
unnamed: JP14.2 (B), U2.13 (11_MOSI_CTX1)
unnamed: JP15.2 (B), U2.14 (12_MISO_MQSL)
unnamed: JP16.2 (B), U2.17 (13_SCK_CRX1_LED)
unnamed: JP17.2 (C), U2.22 (18_A4_SDA0)
unnamed: JP18.2 (C), U2.23 (19_A5_SCL0)
PWM0: JP3.1 (A), U1.2 (0_RX1_CRX2_CS1)
PWM1: JP4.1 (A), U1.3 (1_TX1_CTX2_MISO1)
PWM2: J1.1, U1.4 (2_OUT2)
PWM3: J3.1, U1.5 (3_LRCLK2)
PWM4: J5.1, U1.6 (4_BCLK2)
PWM5: J7.1, U1.7 (5_IN2)
PWM6: J9.1, U1.8 (6_OUT1D)
PWM7/AUDIO_DIN: JP3.3 (B), JP11.1 (A), U1.9 (7_RX2_OUT1A)
PWM8/AUDIO_DOUT: JP4.3 (B), JP12.1 (A), U1.10 (8_TX2_IN1)
PWM9: J8.1, U1.11 (9_OUT1C)
SPI_CS1: J22.4, U1.12 (10_CS_MQSR)
SPI_CS2: J23.4, U1.30 (38_CS1_IN1)
SPI_CS3: J26.4, U1.29 (37_CS)
SPI_CS4: J27.4, JP13.1 (A), U1.28 (36_CS)
SPI_MISO: J22.3, J23.3, J26.3, J27.3, JP15.1 (A), U1.14 (12_MISO_MQSL)
SPI_MOSI: J22.2, J23.2, J26.2, J27.2, JP14.1 (A), U1.13 (11_MOSI_CTX1)
SPI_SCK: J22.5, J23.5, J26.5, J27.5, JP16.1 (A), U1.35 (13_SCK_LED)
UART_RX: J2.1, U1.26 (34_RX8)
UART_TX: J2.2, U1.27 (35_TX8)
Vol_Knob: U1.37 (15_A1_RX3_SPDIF_IN), U2.19 (15_A1_RX3_SPDIF_IN_VOL)

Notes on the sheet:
8x T2000 Thruster PWM
4x SPI Bus
Teensy 4.1
Audio Control
SD Card SPI
Power In
Audio Shield
Jumped to Audio SD
8x I2C Bus

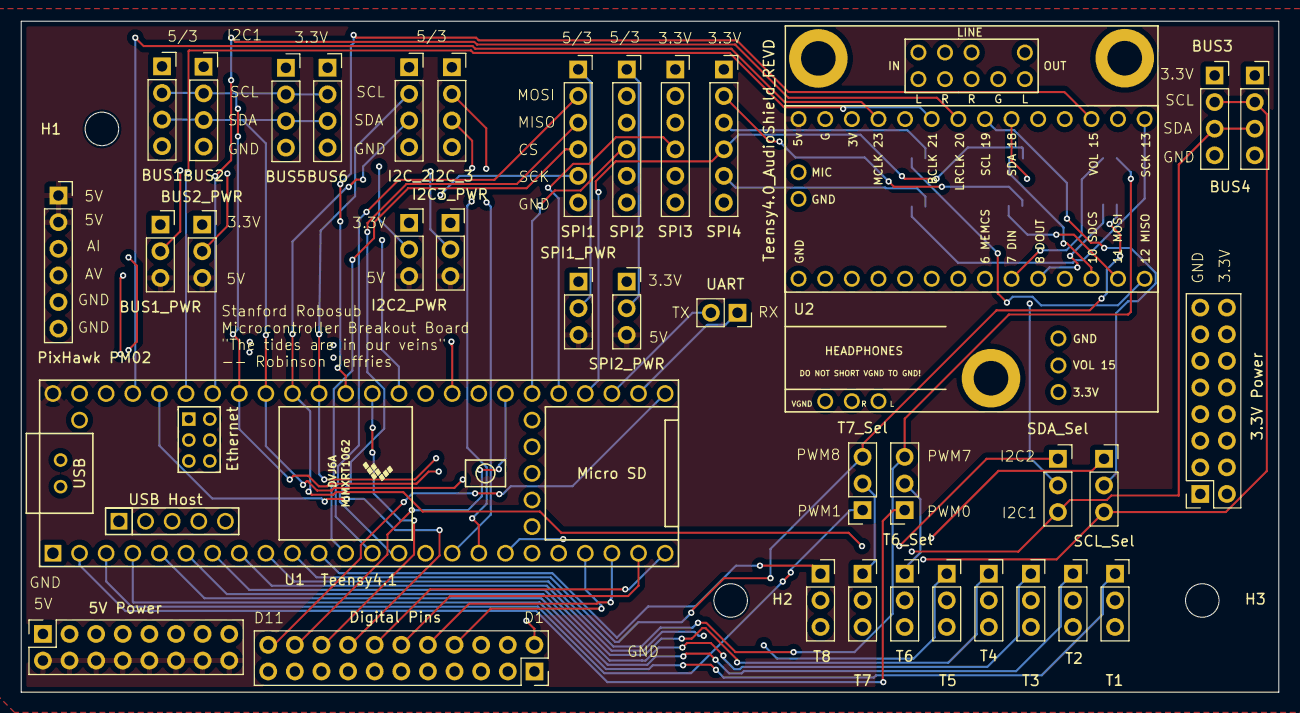
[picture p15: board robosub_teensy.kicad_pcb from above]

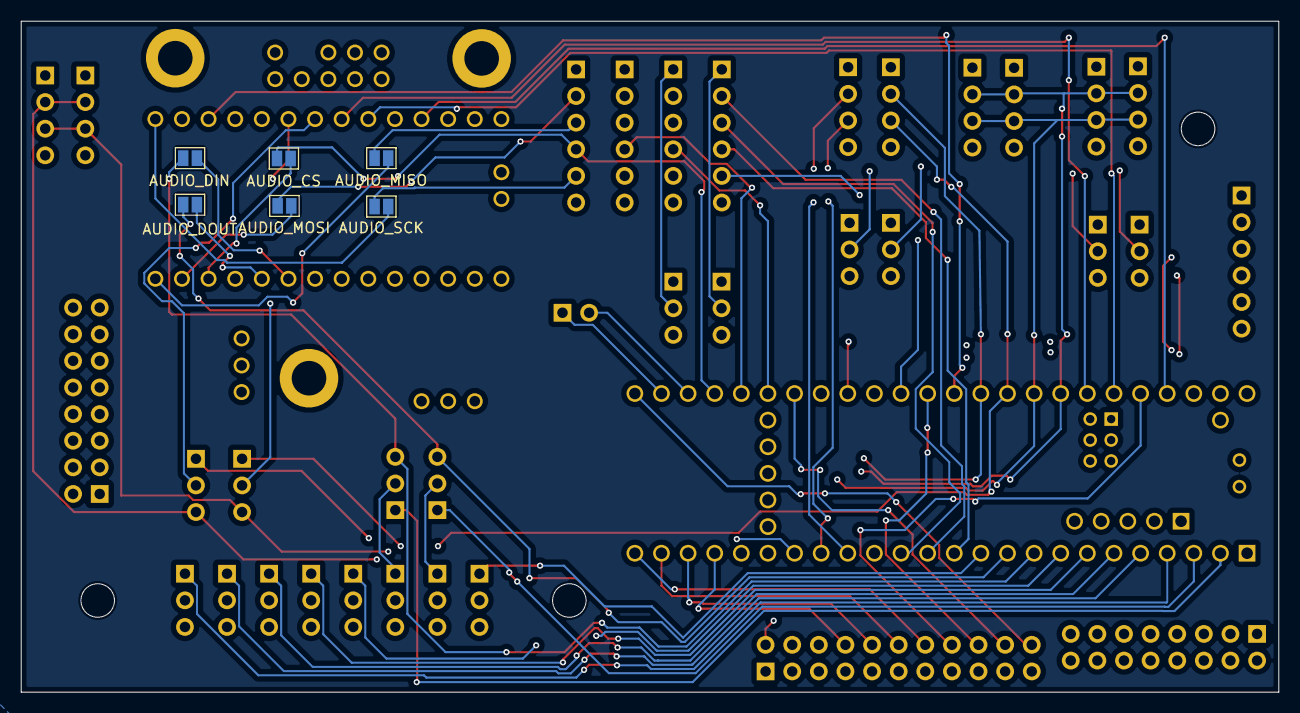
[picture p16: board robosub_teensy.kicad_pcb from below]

Board: 4 copper layers, 120.0 x 64.0 mm, 46 parts (6 on the bottom side), 61 nets.

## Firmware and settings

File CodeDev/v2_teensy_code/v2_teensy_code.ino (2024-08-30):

#include <Servo.h>
#include <Wire.h>
#include <SPI.h>
#include <SD.h>
#include <Adafruit_Sensor.h>
#include <Adafruit_BME280.h>
#include <Adafruit_SSD1306.h>
#include "Adafruit_MCP9808.h"
#include "MS5837.h"

// Constants and configurations
#define KILL_SWITCH_PIN 33
#define KILL_LIGHTS_PIN 39
#define LEAK_DETECT_PIN 14
// 

MS5837 sensor;
Adafruit_SSD1306 display(4);
bool leak = false;
bool surface = true;
int firstWirePin = 22;
int secondWirePin = 21;
int firstVal = 0;
int secondVal = 0;
Servo servos[8];
byte servoPins[] = {2, 3, 4, 5, 6, 7, 8, 9};
char inputBuffer[32];
int bufferPosition = 0;
int displayCounter = 0;
int outerSwitch;
int lightPWM;

// Tempsensors (0x18, 0x19, 0x1A, I2C_Bus_1)
Adafruit_MCP9808 tempsensor1 = Adafruit_MCP9808();
Adafruit_MCP9808 tempsensor2 = Adafruit_MCP9808();
Adafruit_MCP9808 tempsensor3 = Adafruit_MCP9808();

// SD Card
const int SDSelect = BUILTIN_SDCARD;

// Light PWM
// Servo lightServo; 

void setup() {
    Serial.begin(9600);
    configServo();
    configDepthSensor();
    display.begin(SSD1306_SWITCHCAPVCC, 0x3C);
    pinMode(KILL_SWITCH_PIN, INPUT);
    pinMode(KILL_LIGHTS_PIN, OUTPUT);
    digitalWrite(KILL_LIGHTS_PIN, HIGH);
    pinMode(LEAK_DETECT_PIN, INPUT);

    tempsensor1.begin(0x18);
    tempsensor1.setResolution(3);
    tempsensor1.wake();

    tempsensor2.begin(0x19);
    tempsensor2.setResolution(3);
    tempsensor2.wake();

    tempsensor3.begin(0x1A);
    tempsensor3.setResolution(3);
    tempsensor3.wake();

    SD.begin(SDSelect);

}
void loop() {
    handleSerialInput();
    readLeakSensor();
    if (displayCounter >= 80) {
        updateDisplay();

        logTemperatureData();
        displayCounter = 0;
    }
    displayCounter++;
}
void configServo() {
    for (int i = 0; i < 8; i++) {
        servos[i].attach(servoPins[i]);
        servos[i].writeMicroseconds(1500); // Neutral position
    }
}
void configDepthSensor() {
    Wire.begin();
    sensor.setModel(MS5837::MS5837_02BA);
    sensor.init();
    sensor.setFluidDensity(997); // kg/m^3 for freshwater
}
void readLeakSensor() {
    if (!leak) {
        leak = digitalRead(LEAK_DETECT_PIN);
    } else if (leak && surface) {
        floatToSurface();
        surface = false;
    }
}
void readTempSensors(float temps[3]) {
    temps[0] = tempsensor1.readTempC();
    temps[1] = tempsensor2.readTempC();
    temps[2] = tempsensor3.readTempC();
}
void logTemperatureData() {
  // Make a string for assembling the data to log:
  String dataString = "";

  // Get the current time in milliseconds since the program started
  unsigned long currentTime = millis();

  // Append the current time to the data string
  dataString += String(currentTime) + ",";

  // Array to store temperature readings from sensors
  float temps[3];
  readTempSensors(temps);

  // Append each temperature to the data string
  for (int i = 0; i < 3; i++) {
    dataString += String(temps[i], 2);  // Format to 2 decimal places
    if (i < 2) {  // Add a comma after the first two values
      dataString += ",";
    }
  }

  // Open the file for writing
  File dataFile = SD.open("datalog.txt", FILE_WRITE);

  // If the file is available, write to it:
  if (dataFile) {
    dataFile.println(dataString);
    dataFile.close();
    // Print to the serial port too:
    // Serial.println(dataString);
  } else {
    // If the file isn't open, pop up an error:
    // Serial.println("error opening datalog.txt");
  }
}
void floatToSurface() {
    Serial.println("leak detected!! surfacing for 20 seconds");
    for (int i = 0; i < 4; i++) {
        servos[i].writeMicroseconds(1650);
    }
    for (int i = 4; i < 8; i++) {
        servos[i].writeMicroseconds(1500);
    }
    for (int i = 20; i >= 0; i--) {
        Serial.println(i);
        delay(1000);
    }
    for (int i = 0; i < 8; i++) {
        servos[i].writeMicroseconds(1500); // neutral position
    }
}
void handleSerialInput() {
    while (Serial.available() > 0) {
        char inChar = (char)Serial.read();
        if (inChar == '\n' || inChar == '\r') {
            inputBuffer[bufferPosition] = '\0';
            processInput(inputBuffer);
            bufferPosition = 0;
        } else if (bufferPosition < sizeof(inputBuffer) - 1) {
            inputBuffer[bufferPosition++] = inChar;
        }
    }
}
void processInput(char* input) {
    if (strcmp(input, "depth") == 0) {
        handleDepthCommand();
    } else if (strcmp(input, "voltage") == 0) {
        handleVoltageCommand();
    } else {
        int servoNum, val;
        outerSwitch = digitalRead(KILL_SWITCH_PIN);
        if (sscanf(input, "%d %d", &servoNum, &val) == 2 && outerSwitch == LOW && !leak) {
            if (isValidServoCommand(servoNum, val)) {
                setServo(servoNum, val);
                Serial.println("Sucessfully set servo");
            } else {
                Serial.println("Invalid command");
            }
        } else {
            Serial.println("Invalid format");
        }
    }
}
bool isValidServoCommand(int servoNum, int val) {
    return val >= 1100 && val <= 1900 && servoNum >= 2 && servoNum <= 9;
}
void handleDepthCommand() {
    sensor.read();
    Serial.println(String(sensor.pressure(), 2) + " mbar " + String(sensor.temperature(), 2) + " °C " + String(sensor.depth(), 2) + " m");
}
void handleVoltageCommand() {
    firstVal = analogRead(firstWirePin);
    secondVal = analogRead(secondWirePin);
    double current = (firstVal * 120.0) / 1024;
    double voltage = (secondVal * 60.0) / 1024;
    Serial.println(String(current, 2) + " A " + String(voltage, 2) + " V");
}
void setServo(int servoNum, int val) {
    if (servoNum >= 2 && servoNum <= 9) {
        servos[servoNum - 2].writeMicroseconds(val);
    }
}
void updateDisplay() {
    firstVal = analogRead(firstWirePin);
    secondVal = analogRead(secondWirePin);
    double current = (firstVal * 120.0) / 1024;
    double voltage = (secondVal * 60.0) / 1024;
    sensor.read();
    outerSwitch = digitalRead(KILL_SWITCH_PIN);
    if (outerSwitch == 1) {
        configServo();
        if (lightPWM == 1) {
            digitalWrite(KILL_LIGHTS_PIN, LOW);
            lightPWM = 0;
        } else {
            digitalWrite(KILL_LIGHTS_PIN, HIGH);
            lightPWM = 1;
        }
    } else {
        digitalWrite(KILL_LIGHTS_PIN, HIGH);
    }
    String text = String(voltage) + " V, Switch: " + String(outerSwitch) + "\n" +
                  String(sensor.depth(), 2) + " m, " +
                  String(sensor.temperature(), 2) + " °C, " +
                  String(sensor.pressure(), 2) + " mbar";
    displayText(text);
}
void displayText(String text) {
    display.clearDisplay();
    display.setTextSize(1.5);
    display.setTextColor(WHITE);
    display.setCursor(0, 0);
    display.println(text);
    display.display();
}

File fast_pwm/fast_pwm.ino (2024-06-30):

#include <Servo.h>
#include <Wire.h>
#include <SPI.h>
#include <Adafruit_Sensor.h>
#include <Adafruit_BME280.h>
#include <Adafruit_SSD1306.h>
#include "MS5837.h"
MS5837 sensor;
Adafruit_SSD1306 display(4);
// #define BME_SCK 13
// #define BME_MISO 12
// #define BME_MOSI 11
// #define BME_CS 10
// #define SEALEVELPRESSURE_HPA (1013.25)
// Adafruit_BME280 bme; // I2C once the internal humidity sensor is working

int firstWirePin = 22;
int secondWirePin = 21;
int firstVal = 0;
int secondVal = 0;

Servo servo[8];
byte servoPins[] = {2, 3, 4, 5, 6, 7, 8, 9};
char inputBuffer[32]; // Buffer to store incoming serial data
int bufferPosition = 0; // Position in the buffer
int k = 0; // for display updating
int outerSwitch;
int light_pwm;
int switch_debounce = 0;


void setup() {
  Serial.begin(9600);
  config_servo();
  config_depth_sensor();
  display.begin(SSD1306_SWITCHCAPVCC, 0x3C); // start the display
  pinMode(10, INPUT);
  pinMode(12, OUTPUT);
  digitalWrite(12, 1);
  // unsigned status;
  // status = bme.begin();
  // if (!status) {
  //       Serial.println("Could not find a valid BME280 sensor, check wiring, address, sensor ID!");
  //       Serial.print("SensorID was: 0x"); Serial.println(bme.sensorID(),16);
  //       Serial.print("        ID of 0xFF probably means a bad address, a BMP 180 or BMP 085\n");
  //       Serial.print("   ID of 0x56-0x58 represents a BMP 280,\n");
  //       Serial.print("        ID of 0x60 represents a BME 280.\n");
  //       Serial.print("        ID of 0x61 represents a BME 680.\n");
  //       while (1) delay(10);
  // }
}

void config_servo() {
  for (int i = 0; i < 8; i++) {
    servo[i].attach(servoPins[i]);
    servo[i].writeMicroseconds(1500); // Default neutral position
  }
}

void config_depth_sensor(){
  Wire.begin();
  sensor.setModel(MS5837::MS5837_02BA); // model number for Bar02
  sensor.init();
  sensor.setFluidDensity(997); // kg/m^3 (997 freshwater, 1029 for seawater)
}


void loop() {
  while (Serial.available() > 0) {
    char inChar = (char)Serial.read();
    if (inChar == '\n' || inChar == '\r') { // End of one command, handle both carriage return and newline
      inputBuffer[bufferPosition] = '\0'; // Null-terminate the string
      process_input(inputBuffer);
      bufferPosition = 0; // Reset buffer for the next command
      
    } else {
        if (bufferPosition < sizeof(inputBuffer) - 1) { // Prevent buffer overflow
          inputBuffer[bufferPosition++] = inChar;
        }
    }
  }
  if (k >= 80) {
    firstVal = analogRead(firstWirePin); // current sensor
    secondVal = analogRead(secondWirePin);
    double current = (firstVal * 120.0) / 1024;
    double voltage = (secondVal * 60.0) / 1024;

    sensor.read(); // presure sensor

    outerSwitch = digitalRead(10);

    if (outerSwitch == 1) {
      if (switch_debounce == 0) {
        config_servo();
        switch_debounce = 0; // set to one to implement debouncing
      }
      if (light_pwm == 1) {
        digitalWrite(12, 0);
        light_pwm = 0;
      } else {
        digitalWrite(12, 1);
        light_pwm = 1;
      }
    } else {
      digitalWrite(12, 1);
      switch_debounce = 0;
    }

    String text = String(voltage) + " V " + "Switch: " + String(outerSwitch) + "\n" + String(sensor.depth(), 2) + " mDeep\n";
    displayText(text);
    k = 0;
  }

  k = k + 1;
}
void process_input(char *input) {
  if (strcmp(input, "depth") == 0) {
    handle_depth_command();
  } else if (strcmp(input, "voltage") == 0) {
    handle_voltage_command();
  } else {
    // Handle numerical servo control
    int servoNum, val;
    if (sscanf(input, "%d %d", &servoNum, &val) == 2) {
      if (val >= 1100 && val <= 1900 && servoNum >= 2 && servoNum <= 9) {
        set_servo(servoNum, val);
      } else {
        Serial.println("not valid");
      }
    } else {
      Serial.println("Invalid format");
    }
  }
}

void handle_depth_command() {
  sensor.read();
  
  Serial.println(String(sensor.pressure(), 2) + "mbar " + String(sensor.temperature(), 2) + "C " + String(sensor.depth(), 2) + "mDeep ");
}

void handle_voltage_command() {
  firstVal = analogRead(firstWirePin);
  secondVal = analogRead(secondWirePin);
  double current = (firstVal * 120.0) / 1024;
  double voltage = (secondVal * 60.0) / 1024;
  Serial.println(String(current, 2) + "A " + String(voltage, 2) + "V");
}

void set_servo(int servoNum, int val) {
  if (servoNum < 2 || servoNum > 9) return; // Out of valid servo range
  servo[servoNum - 2].writeMicroseconds(val); // Adjust servo position
}

void displayText(String text) {
  display.clearDisplay();
  display.setTextSize(1.5);
  display.setTextColor(WHITE);
  display.setCursor(0,0);
  display.println(text);
  display.display();
}

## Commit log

2024-04-26 thrust_pwm.ino
    fix PWM addressing, working version
    [thrust_pwm.ino]
2024-04-26 update[readme for PWM]
2024-05-03 including board EDA
    [1135333.step, AUIR3241STR.step, INA300AIDSQT.step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]
2024-05-11 Create thrust_pwm_sensor.ino
    pwm assignment code that includes reading from voltage and pressure sensor
2024-05-17 test pwm in terminal
2024-05-25 RC controller code
    This is the code to control motors through RC controller (has not been tested yet with teensy wired to motors)
2024-05-27 ryota's i2c code
2024-05-27 include display and light/switch functionality
2024-06-30 save[power distribution board rev1]
2024-06-30 rename and reorganize
    [1135333.step, AUIR3241STR.step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]
2024-06-30 power rev2[fix diodes, ground loop, silkscreen]
    [Robosub_Power.kicad_pcb, Robosub_Power.kicad_sch]
2024-06-30 rev2 [final]
    [Robosub_Power.kicad_pcb]
2024-07-01 rev2 -ok2fab
    [Robosub_Power-B_Cu.gbr, Robosub_Power-B_Mask.gbr, Robosub_Power-B_Paste.gbr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]
2024-07-03 restructuring github
    [1135333.step, AUIR3241STR.step, Compute_Power_Board.kicad_pcb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]
2024-07-03 fix[software kill switch]
2024-07-13 adding ryota board
    [robosub_teensy.kicad_pcb, robosub_teensy.kicad_sch]
2024-07-14 teensy board schematic
    [robosub_teensy.kicad_pcb, robosub_teensy.kicad_sch]
2024-07-15 v1 ok2fab
    [Robosub_Power.kicad_pcb, Robosub_Power.kicad_sch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]
2024-08-29 adding ryota leak detect
    [fast_pwm_with_display.ino, v2_teensy_code.ino]
2024-10-23 for Fabi
    [Power_Distribution.kicad_pcb, Power_Distribution.kicad_sch]
2024-10-30 draft of connecting board with current sensors
    I'm still waiting to get an email back for the footprint of the connector pins but i have a good one saved.
2024-11-07 Final Power Dist Board
    [Power_Distribution.kicad_pcb, Power_Distribution.kicad_sch]
2024-11-07 pushing current management board
    [Power_Management.kicad_pcb, Power_Management.kicad_sch]
2024-11-07 Finished and Tested
    [Power_Distribution.kicad_pcb]
2024-11-15 done with management
    [AND_GATES.kicad_sch, Battery_interfaces.kicad_sch, FET_control_relay.kicad_sch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]
2024-11-15 good spot
    [Power_Distribution-B_Cu.gbr, Power_Distribution-B_Mask.gbr, Power_Distribution-B_Paste.gbr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]
2024-11-28 BOM changes
    [Power_Distribution.kicad_sch, buck_boost.kicad_sch, power_distribution_gen2_BOM.csv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]
2025-01-29 pcb to fit dimensions
    [Power_Distribution.kicad_pcb]

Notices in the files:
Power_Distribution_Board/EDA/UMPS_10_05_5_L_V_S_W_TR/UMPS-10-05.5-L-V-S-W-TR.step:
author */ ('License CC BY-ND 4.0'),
